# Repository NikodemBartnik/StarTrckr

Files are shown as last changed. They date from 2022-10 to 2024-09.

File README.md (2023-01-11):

## StarTracker - 3 axis astrophotography tracking solution

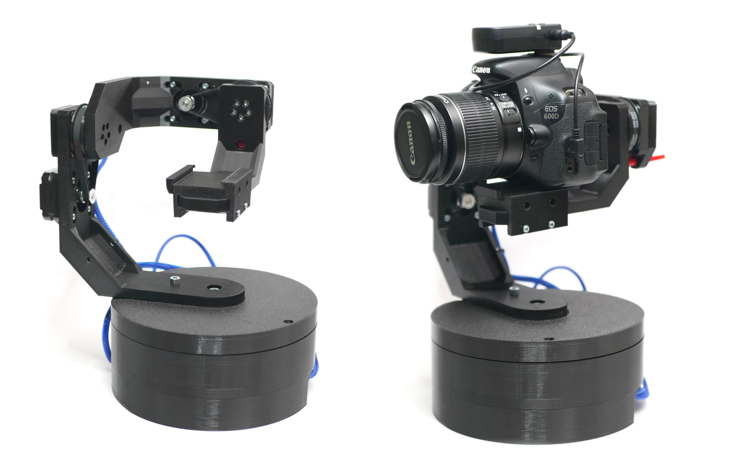
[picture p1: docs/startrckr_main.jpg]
startracker image


**Project is still in development and it may change!**<br>
Welcome to the StarTrckr project, an innovative solution to the problem of tracking in astrophotography. The goal of this project is to get over the limits of conventional tracking techniques so that hobbyists and enthusiasts can more easily take beautiful pictures of the night sky. Additionaly this construction enables for easier tracking of other objects (for example satellites) but the feature is not implemented yet.

A further benefit of the design is that it can be completely 3D printed, making it simple for everyone to construct and modify their own tracking device. It is planned to design an additional pro version that features steel parts for increased stiffness of the construction but 3D printed version will always stay as the bassis thats accesible and easy to replicate for everyone.

Since he was a young child, Nikodem Bartnik, the project's creator, has been fascinated about observing the night sky and space in general.  He is constantly searching for new ways to enhance the system and make it easier to use for users of all levels. At the same time he is into developing various open source projects and documenting the journeys of creating them on his YouTube channel. Additionaly is a part of Silesian Aerospace Technologies science club where together with friends he develops high altitude balloons, rockets and cubesat subsystems.

Designed by [Nikodem Bartnik](https://www.youtube.com/nikodembartnik). 

## Mechanics
Different design approaches have been considered and in the end multiple designs were created. Some of those are presented in the image below.
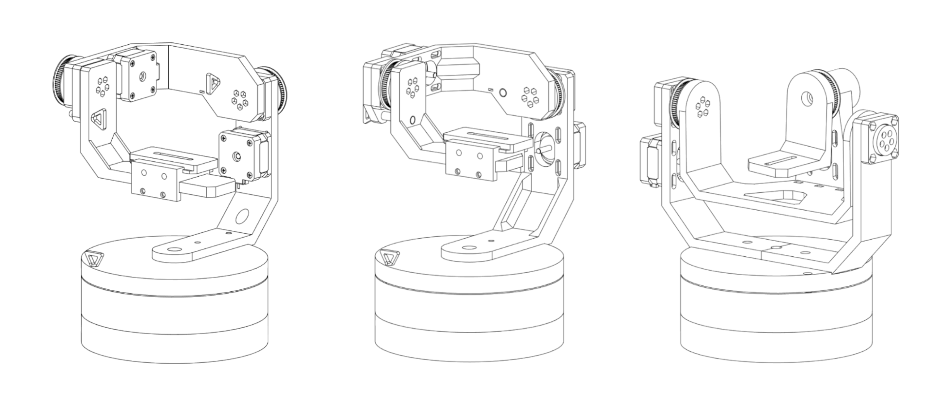
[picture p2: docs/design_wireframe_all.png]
StarTrckr designs

Most parts have been 3D printed and only a few additional parts like bearings, screws and motors are neccesary from the mechanical point of view. As of writing this readme there are three versions included in cad folder (v2, v3 nad v4). At this point v3 is prefered version and the one that is currently tested. Following list of printed parts reffers to v3.
| Name | Amount |
|---|---|
| arm1.3mf | 1 |
| arm2.3mf | 1 |
| arm3.3mf | 1 |
| base_pcb_box.3mf | 1 |
| base_motor_holder.3mf| 1 |
| base_gear.3mf | 1 |
| base_bearing_cap.3mf | 1 |
| base_gear_small.3mf  | 1 |
| gt2_pulley.3mf | 2 |
| shaft.3mf | 2 |
| shaft_cap.3mf | 2 |
| bearing_flap.3mf | 2 |
| quick_release_plate.3mf| 1 |
| quick_release1.3mf | 1 |
| quick_release2.3mf | 1 |
| pin.3mf | 3 |

List of additional parts needed for the mechanical assembly:
| Name | Amount | Description 
|---|---|---|
| Stepper motor 17HS08-1004S | 3 | Pancake type stepper motor, height: 20mm |
| 6205 bearing | 2 | ball bearing |
| 6804 bearing | 2 | ball bearing |
| GT2 belt 200mm | 2 | 6mm wide |
| GT2 pulley | 2 | 16 teeth |
| M6x60 screw | 1 |  |
| M6 nut | 1 | |
| M5 screws | a lot | lengths and amounts depend a lot on the version you are building |
| M5 nuts | a lot | |
| M3 screws | a lot | lengths and amounts depend a lot on the version you are building |
| M3 nuts | a lot | |

## Electronics
In the pcb folder all files regarding electronics for the project can be found. Everything was designed with KiCad, there is the schematic and PCB layout together with zip archives with gerber files for production and schematic in png format. Here is a table with all components required to assemble the PCB.
| Name | Amount | Description 
|---|---|---|
| RP2040 | 1 | Raspberry Pi microcontroller |
| A4988 | 3 | stepper driver, TMC2209 can be use as an upgrade to increase the accuracy |
| W25Q32JVSS | 1 | Flash memory |
| USB socket | 1 | type B |
| LM1117 | 1 | 3.3V linear voltage regulator |
| LED | 3 | size: 0805 preferably different color for each |
| Buzzer | 1 | THT, 12mm |
| 12MHz crystal | 1 | size: 5032 |
| 27 $\Omega$ resistor| 2 | size: 0603 |
| 100 $\Omega$ resistor|3 | size: 0603 |
| 1k $\Omega$ resistor | 2 | size: 0603 |
| 10k $\Omega$ resistor| 1 | size: 0603 |
| 27pF capacitor | 2 | size: 0603 |
| 1uF capacitor | 2 | size: 0603 |
| 10uF capacitor | 3 | size: 0603 |
| 100nF capacitor | 10 | size: 0603 |
| 2 pin screw terminal| 1 | |
| Some pin headers | | female and male, raster 2.54mm |

## Open Source
The StarTracker project is open-source, and the author welcomes feedback and contributions from the community. They believe that by sharing the project, they can help others to achieve the same level of success in capturing images of the night sky. If you are interested in building your own StarTrckr, the project's Github repository includes detailed instructions and all the necessary files to get started. Project was created as a bachelor thesis project at Silesian University of Technology and the created thesis can also be found in the repository as a PDF where one can read in depth about the research, problems and detailed explantion about the design process and decisions. 

## Software and firmware
Both were developed with Python programming language. As for now designed just as MVP to test basic functionality of the tractor will hopefully be developed more in the future.

## Testing
Example image untracked, f/5.6, ISO200, 600s, 55mm, Canon 600D after editing:
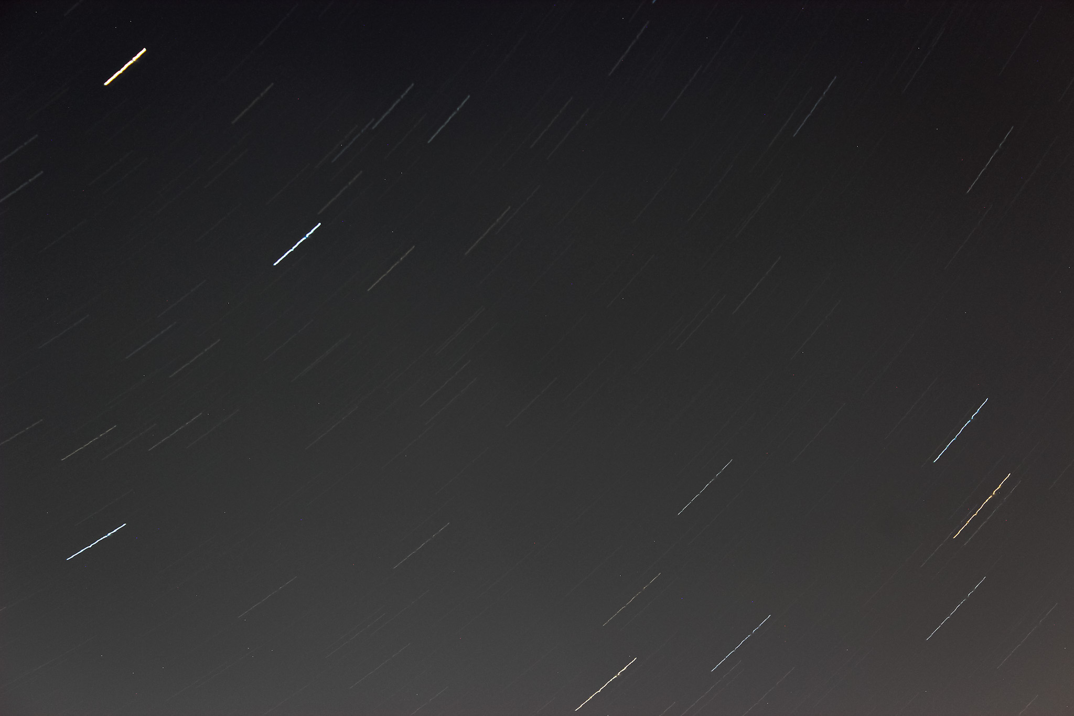
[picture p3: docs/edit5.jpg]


Example image with tracking enabled, same settings, camera and lens:

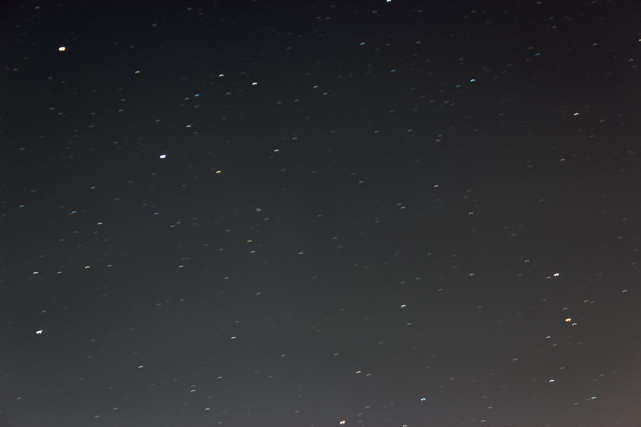
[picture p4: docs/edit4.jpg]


## Build Instruction
- todo 

## Project logo
<br>
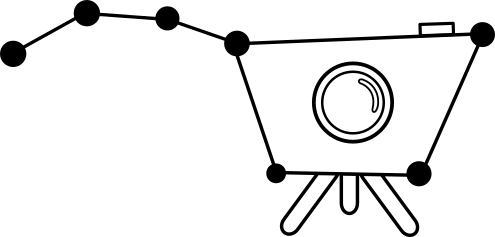
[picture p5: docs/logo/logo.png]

<br><br>

## About the author
Since I was a young child, I have been fascinated about observing the night sky and space in general. I am into developing various open source projects and documenting the journeys of creating them on my YouTube channel. Additionaly I am a part of Silesian Aerospace Technologies science club where together with friends we develop high altitude balloons, rockets and cubesat subsystems.

I hope you enjoy using the StarTracker and are able to capture stunning images of the night sky with it. The StarTracker project is an ongoing effort, and I am always looking for ways to improve it. Feel free to contact me or contribute to the project if you have any ideas or suggestions. Together, we can make astrophotography more accessible and enjoyable for everyone!

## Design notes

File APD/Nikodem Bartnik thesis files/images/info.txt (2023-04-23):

IMG_8831.JPG - tracked, f/5.6, ISO800, 240s, 55mm
IMG_8833.JPG - untracked, f/5.6, ISO800, 240s, 55mm
IMG_8858.JPG - tracked, f/5.6, ISO200, 600s, 55mm
IMG_8859.JPG - untracked, f/5.6, ISO200, 600s, 55mm
stacking_test.jpg - 22 90s exposures stacked together

_edit - versions edited with Lightroom

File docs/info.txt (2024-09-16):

IMG_8831.JPG - tracked, f/5.6, ISO800, 240s, 55mm
IMG_8833.JPG - untracked, f/5.6, ISO800, 240s, 55mm
IMG_8856.JPG - tracked, f/5.6, ISO200, 300s, 55mm
IMG_8857.JPG - untracked, f/5.6, ISO200, 300s, 55mm
IMG_8858.JPG - tracked, f/5.6, ISO200, 600s, 55mm
IMG_8859.JPG - untracked, f/5.6, ISO200, 600s, 55mm
IMG_8859.JPG to IMG_8883.JPG - tracked, f/5.6, ISO200, about 90s, 55mm

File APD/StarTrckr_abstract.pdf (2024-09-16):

### StarTrckr - 3 axis open-source night sky tracking device

Nikodem Bartnik
Silesian University of Technology, Poland

## Abstract

With advancements in digital photography and high-end equipment becoming less expensive, more and more amateurs are getting into astrophotography. Some of the work can be done with just a camera and a tripod but taking more advanced pictures, of objects that are light years away, require special equipment like star trackers, able to precisely compensate for Earth’s rotation, to capture long exposure images of the night sky. Usually, the equipment is expensive; thus, most amateurs can not afford it.

The aim of the project is to design and build an inexpensive, easy-to-build, and open-source star tracker. Relying on popular components that are easy to buy worldwide and 3D printed parts. The project’s reduction in cost and availability is just one component. The actual innovation of the approach is the use of a 3-axis system in conjunction with special algorithms to streamline workflow for the user as well as enable further advancement and facilitate tracking of other objects. StarTrckr is not mechanically aligned with the Earth’s rotation axis, unlike conventional solutions but it is also not susceptible to the issue of field rotation. The system can become totally autonomous, eliminating the need for manual polar alignment, with a few extra sensors added that are not present in the current version but are planned for the future.

Project was developed from scratch solely by the author including mechanical design, electronics design, and programming. Before the design stage began author performed research to find similar solutions and parts best suitable for the project. In order to test and validate the system’s performance, field tests were conducted at the very end and sample long exposure photos up to 600 seconds long were obtained.

StarTrckr was developed as a bachelor thesis project at the Silesian University of Technology and was successfully defended in February 2023. Further development of the projects is planned by the author to create a completely automatic solution and improve the biggest flows of the design. Since the beginning of the project, it was decided that it will be open source and shared with everyone for free to contribute to the development of astrophotography. All files and description of the project can be found on GitHub where it is regularly updated as the work progresses.

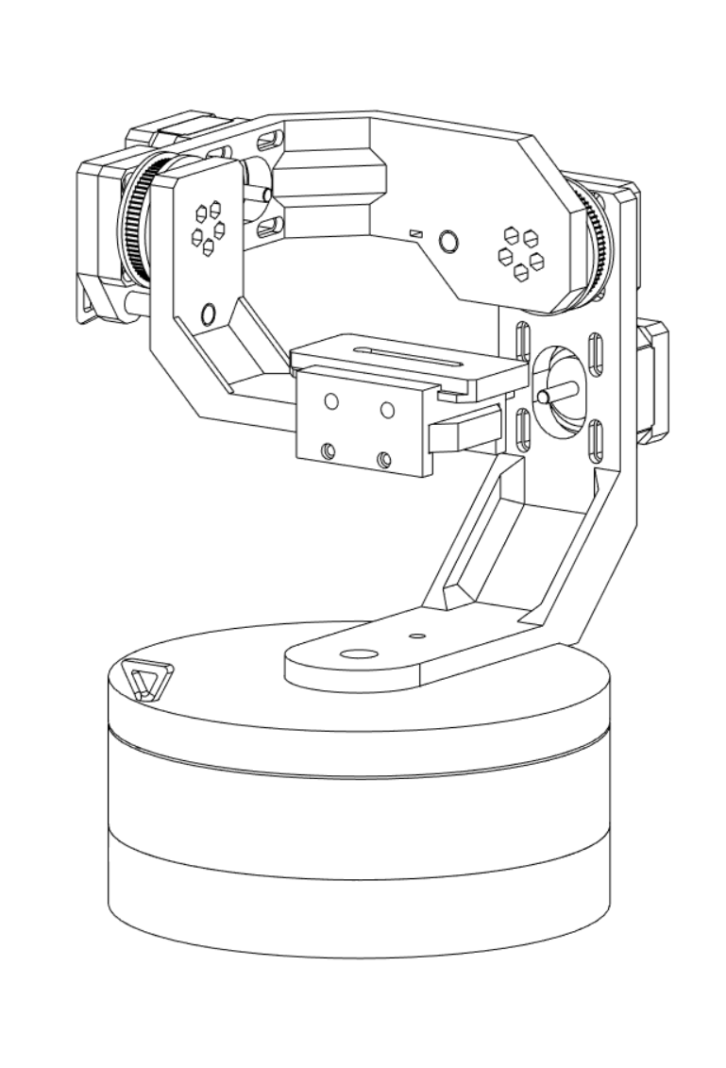
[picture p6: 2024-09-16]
docs/thesis/design/design_wireframe_v3.png

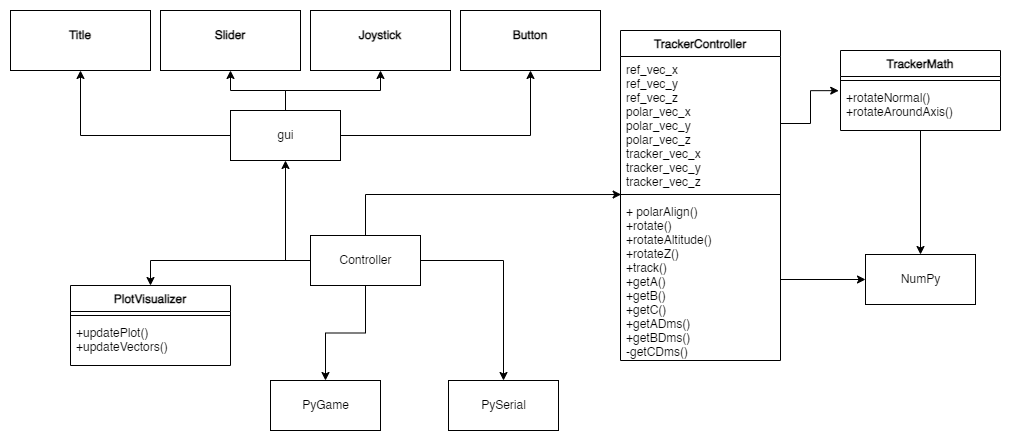
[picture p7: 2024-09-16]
docs/thesis/desktop_software_uml.png

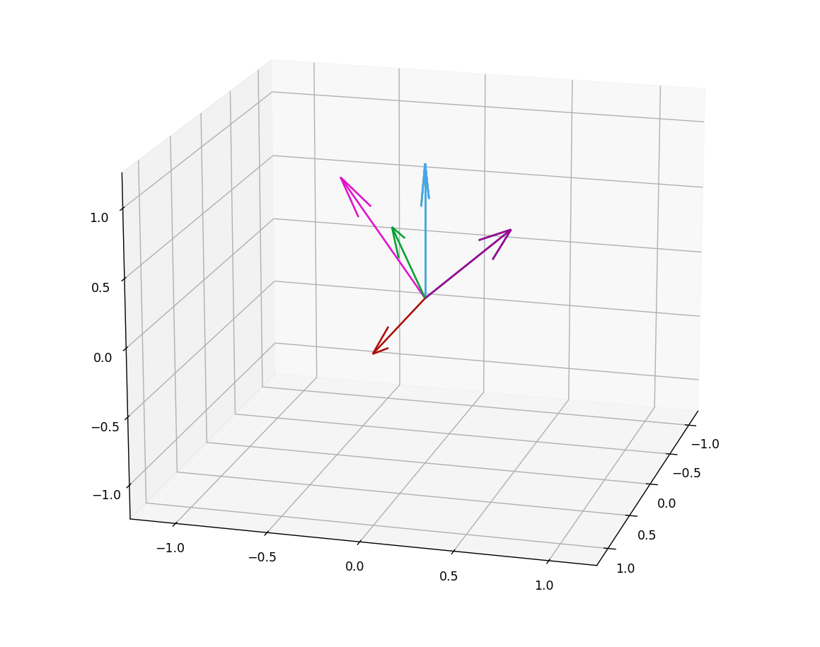
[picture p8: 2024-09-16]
docs/thesis/plot_vectors_2.png

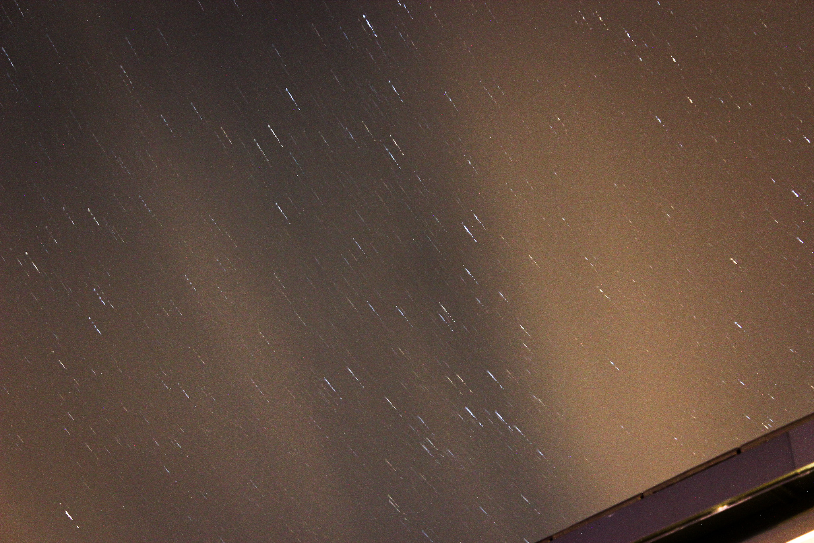
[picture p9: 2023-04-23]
APD/Nikodem Bartnik thesis files/images/IMG_8833_edit.jpg

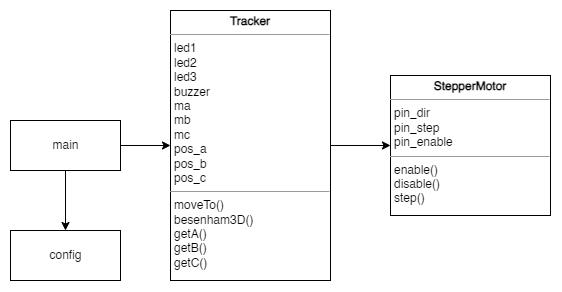
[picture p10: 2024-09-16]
docs/thesis/firmware_uml.png

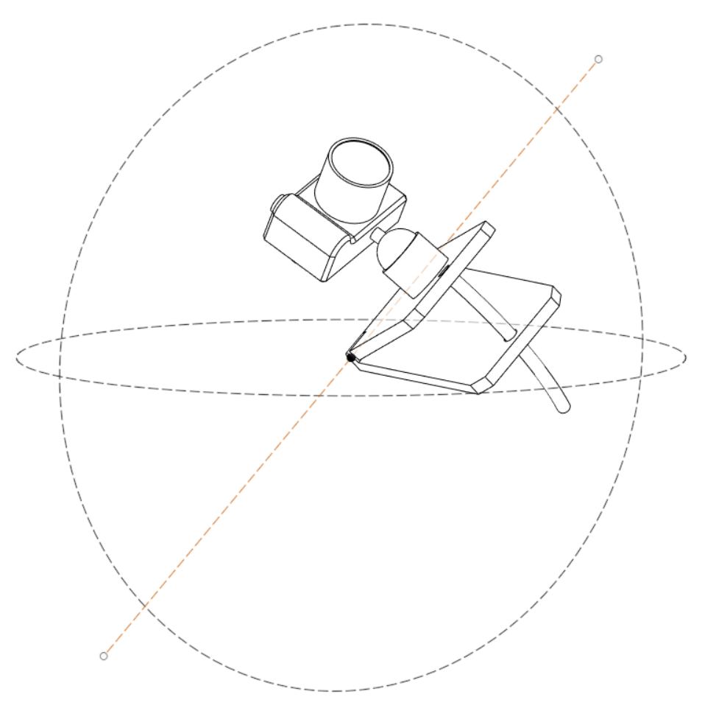
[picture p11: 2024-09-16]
docs/thesis/barndoortracker.png

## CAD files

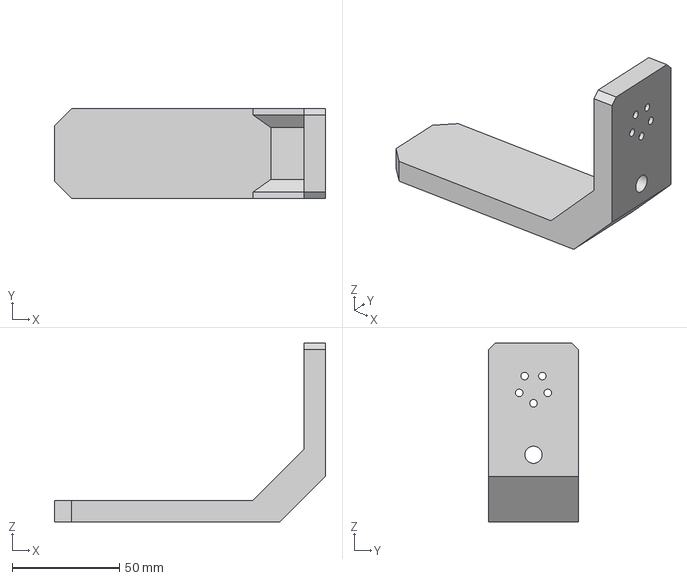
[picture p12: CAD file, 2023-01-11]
APD/Nikodem Bartnik thesis files/3d printed parts/arm3.3mf
126.2 x 42.0 x 83.2 mm

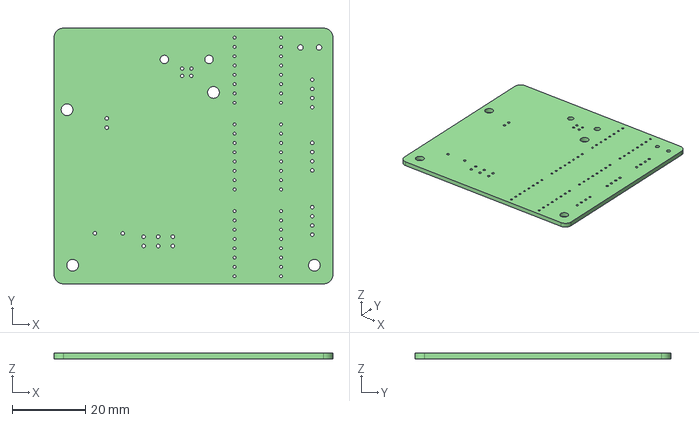
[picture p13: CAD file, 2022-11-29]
APD/Nikodem Bartnik thesis files/pcb/startrckr_pcb.step
76.2 x 69.9 x 1.60 mm

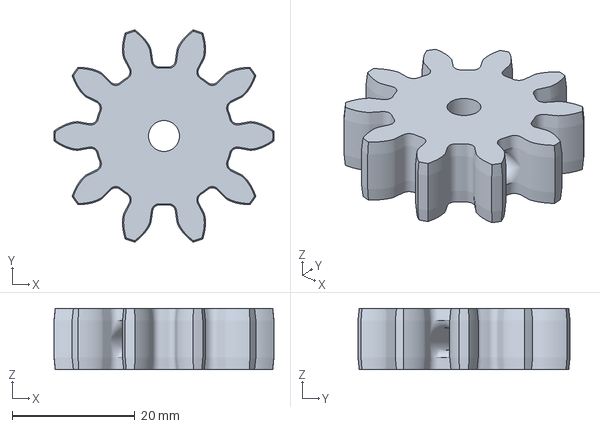
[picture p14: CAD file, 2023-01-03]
cad/v4/base gear small.3mf
35.8 x 34.5 x 10.0 mm

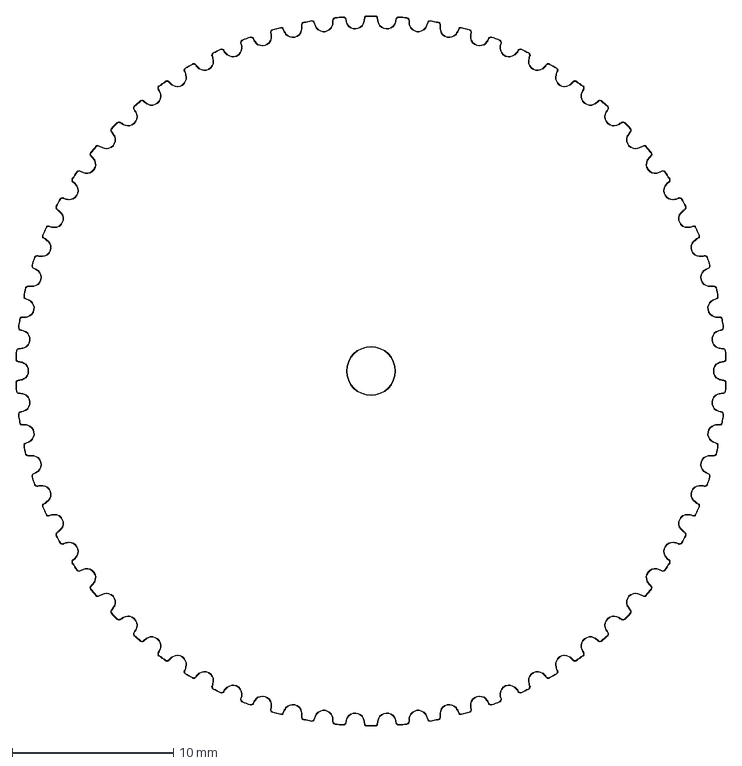
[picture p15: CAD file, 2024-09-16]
docs/gt2 gear/1.dxf
44.1 x 44.1 mm

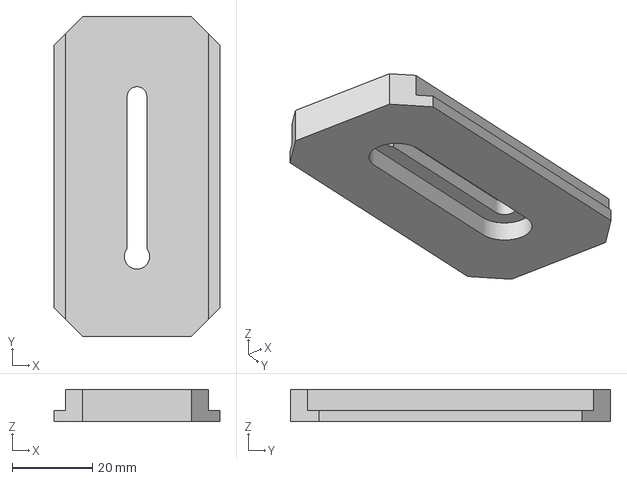
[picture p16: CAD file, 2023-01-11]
APD/Nikodem Bartnik thesis files/3d printed parts/quick release plate.3mf
41.4 x 80.0 x 8.00 mm

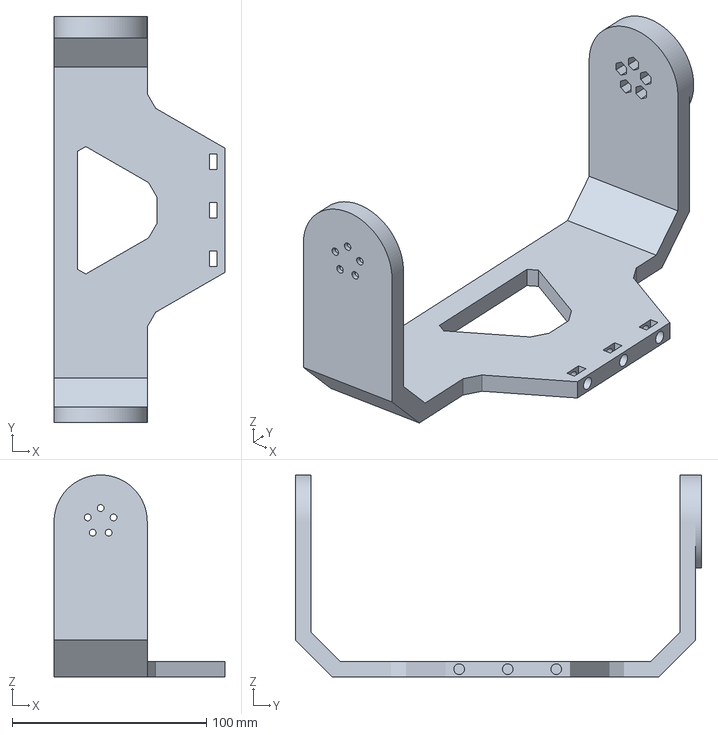
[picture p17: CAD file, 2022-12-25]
cad/v4/arm2.3mf
88.0 x 209.1 x 104.0 mm

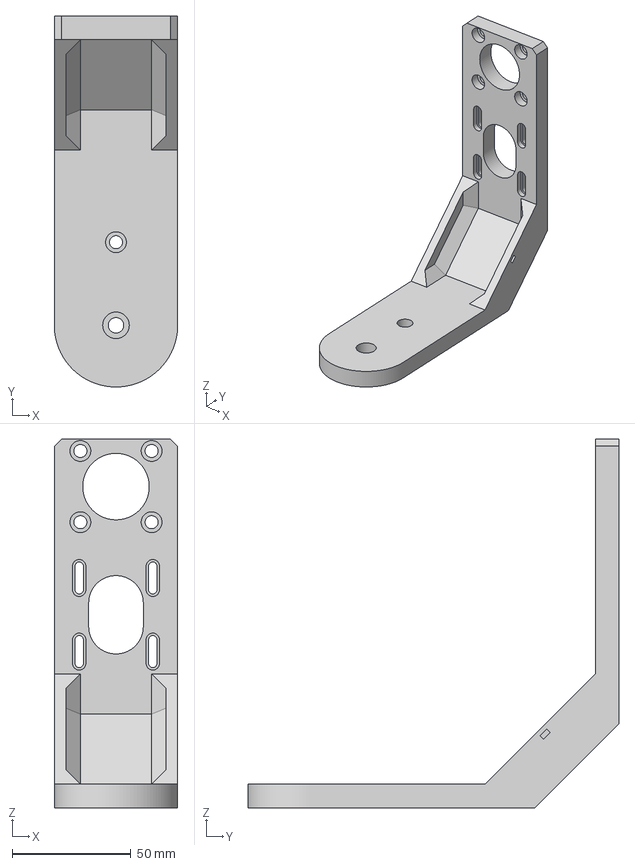
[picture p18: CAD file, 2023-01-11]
APD/Nikodem Bartnik thesis files/3d printed parts/arm1.3mf
52.0 x 156.3 x 155.4 mm

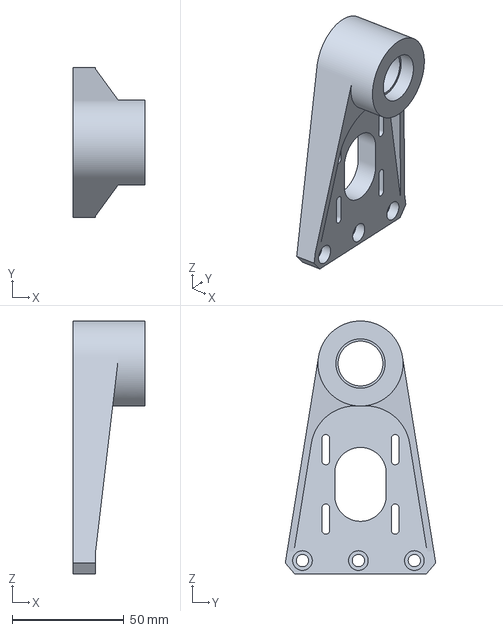
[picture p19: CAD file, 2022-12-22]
cad/v4/rotator plate.3mf
32.0 x 67.2 x 113.0 mm

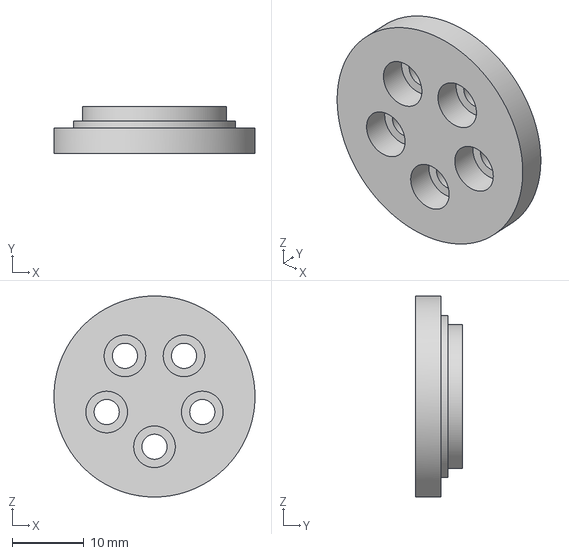
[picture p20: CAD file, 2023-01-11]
APD/Nikodem Bartnik thesis files/3d printed parts/shaft2.3mf
28.0 x 6.50 x 28.0 mm

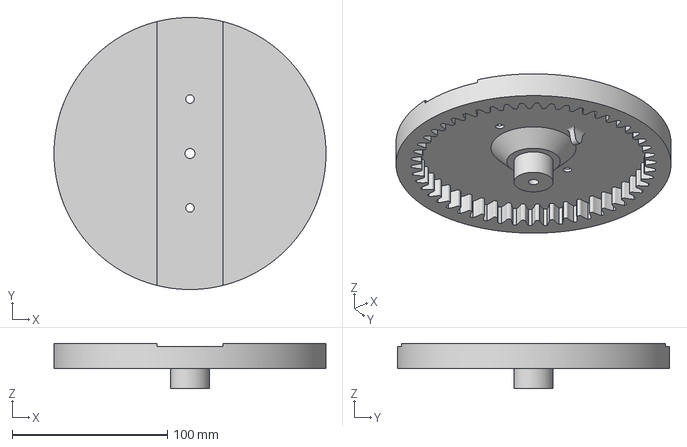
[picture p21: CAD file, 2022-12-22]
cad/v4/base gear.3mf
175.0 x 175.0 x 29.0 mm

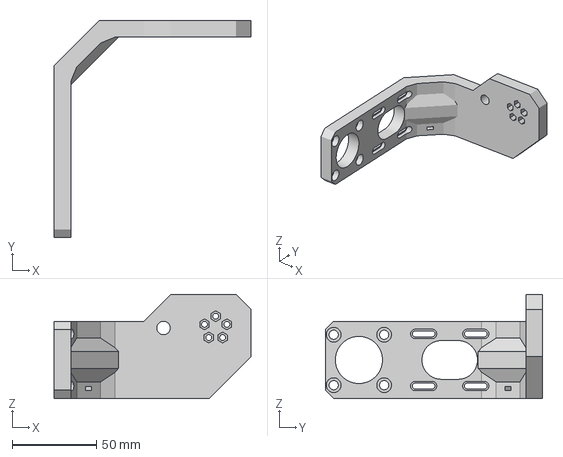
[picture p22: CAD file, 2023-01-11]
APD/Nikodem Bartnik thesis files/3d printed parts/arm2.3mf
117.2 x 129.3 x 62.0 mm

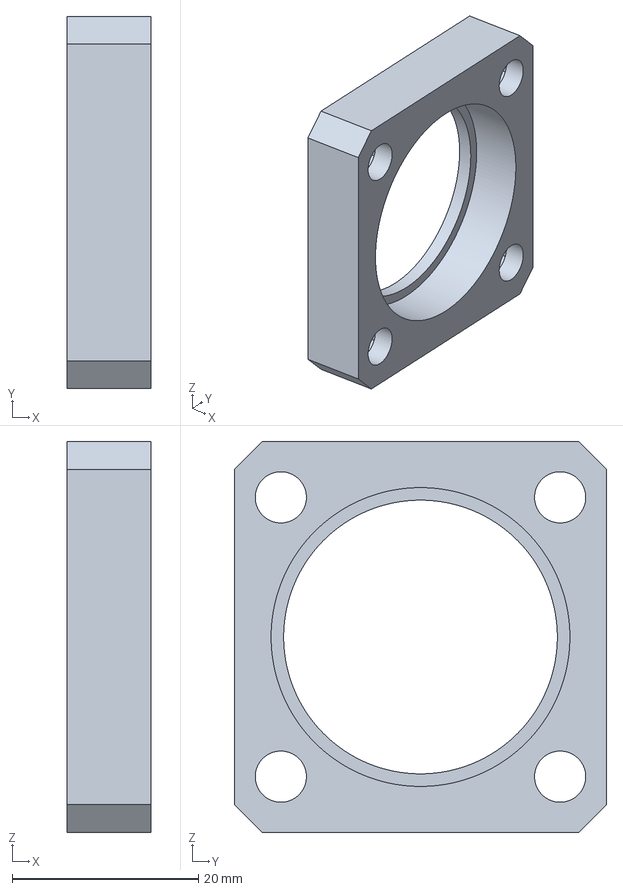
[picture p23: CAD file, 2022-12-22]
cad/v4/bearing flap.3mf
9.00 x 40.0 x 42.0 mm

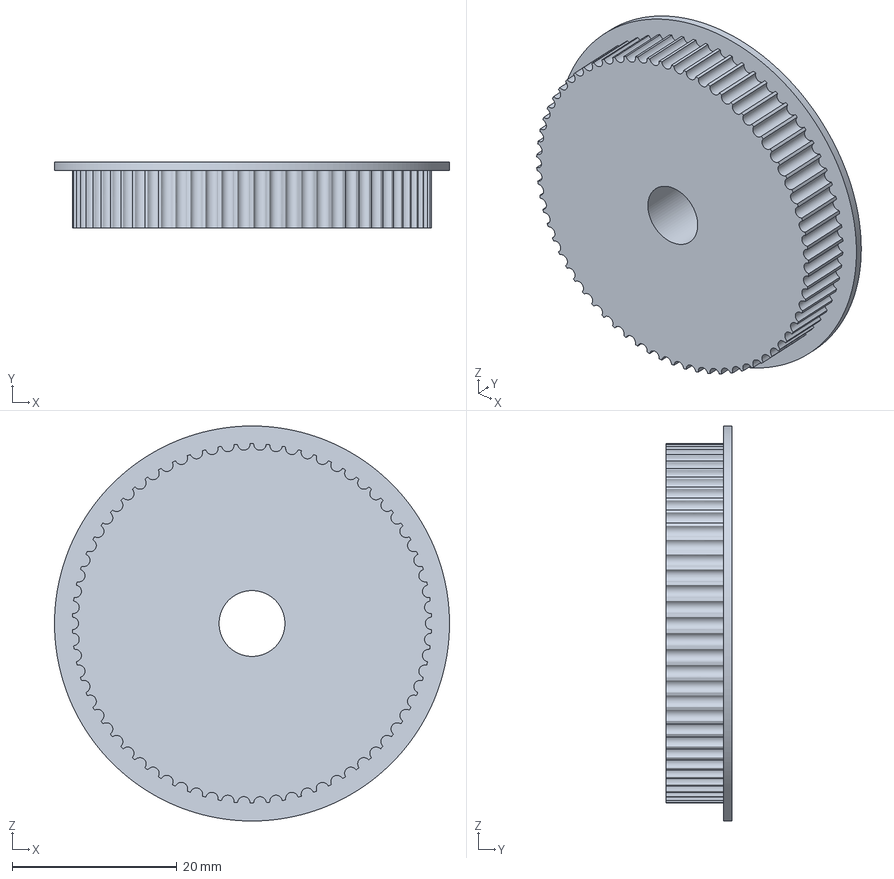
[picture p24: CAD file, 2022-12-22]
cad/v4/rotator pulley.3mf
48.0 x 8.00 x 48.0 mm

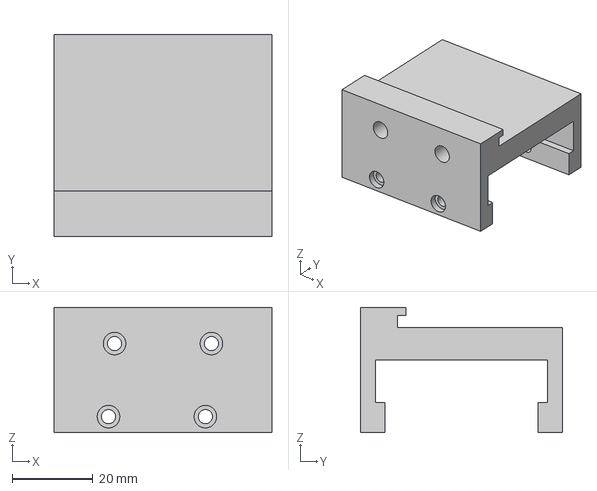
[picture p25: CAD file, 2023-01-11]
APD/Nikodem Bartnik thesis files/3d printed parts/quick release 1.3mf
54.0 x 50.0 x 31.0 mm

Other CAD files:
APD/Nikodem Bartnik thesis files/3d printed parts/base gear.3mf
cad/v4/base motor holder.3mf
APD/Nikodem Bartnik thesis files/3d printed parts/base bearing cap.3mf
cad/v4/arm1_1.3mf
APD/Nikodem Bartnik thesis files/3d printed parts/base PCB box.3mf
APD/Nikodem Bartnik thesis files/3d printed parts/base gear small.3mf
APD/Nikodem Bartnik thesis files/3d printed parts/base motor holder.3mf
APD/Nikodem Bartnik thesis files/3d printed parts/bearing flap.3mf
APD/Nikodem Bartnik thesis files/3d printed parts/gt2 pulley.3mf
APD/Nikodem Bartnik thesis files/3d printed parts/pin.3mf
APD/Nikodem Bartnik thesis files/3d printed parts/quick release 2.3mf
APD/Nikodem Bartnik thesis files/3d printed parts/shaft1.3mf
cad/v2/arm1.3mf
cad/v2/arm2.3mf
cad/v2/arm3.3mf
cad/v2/base gear small.3mf
cad/v2/base gear.3mf
cad/v2/bearing flap.3mf
cad/v2/gt2 pulley.3mf
cad/v2/quick release 1.3mf
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

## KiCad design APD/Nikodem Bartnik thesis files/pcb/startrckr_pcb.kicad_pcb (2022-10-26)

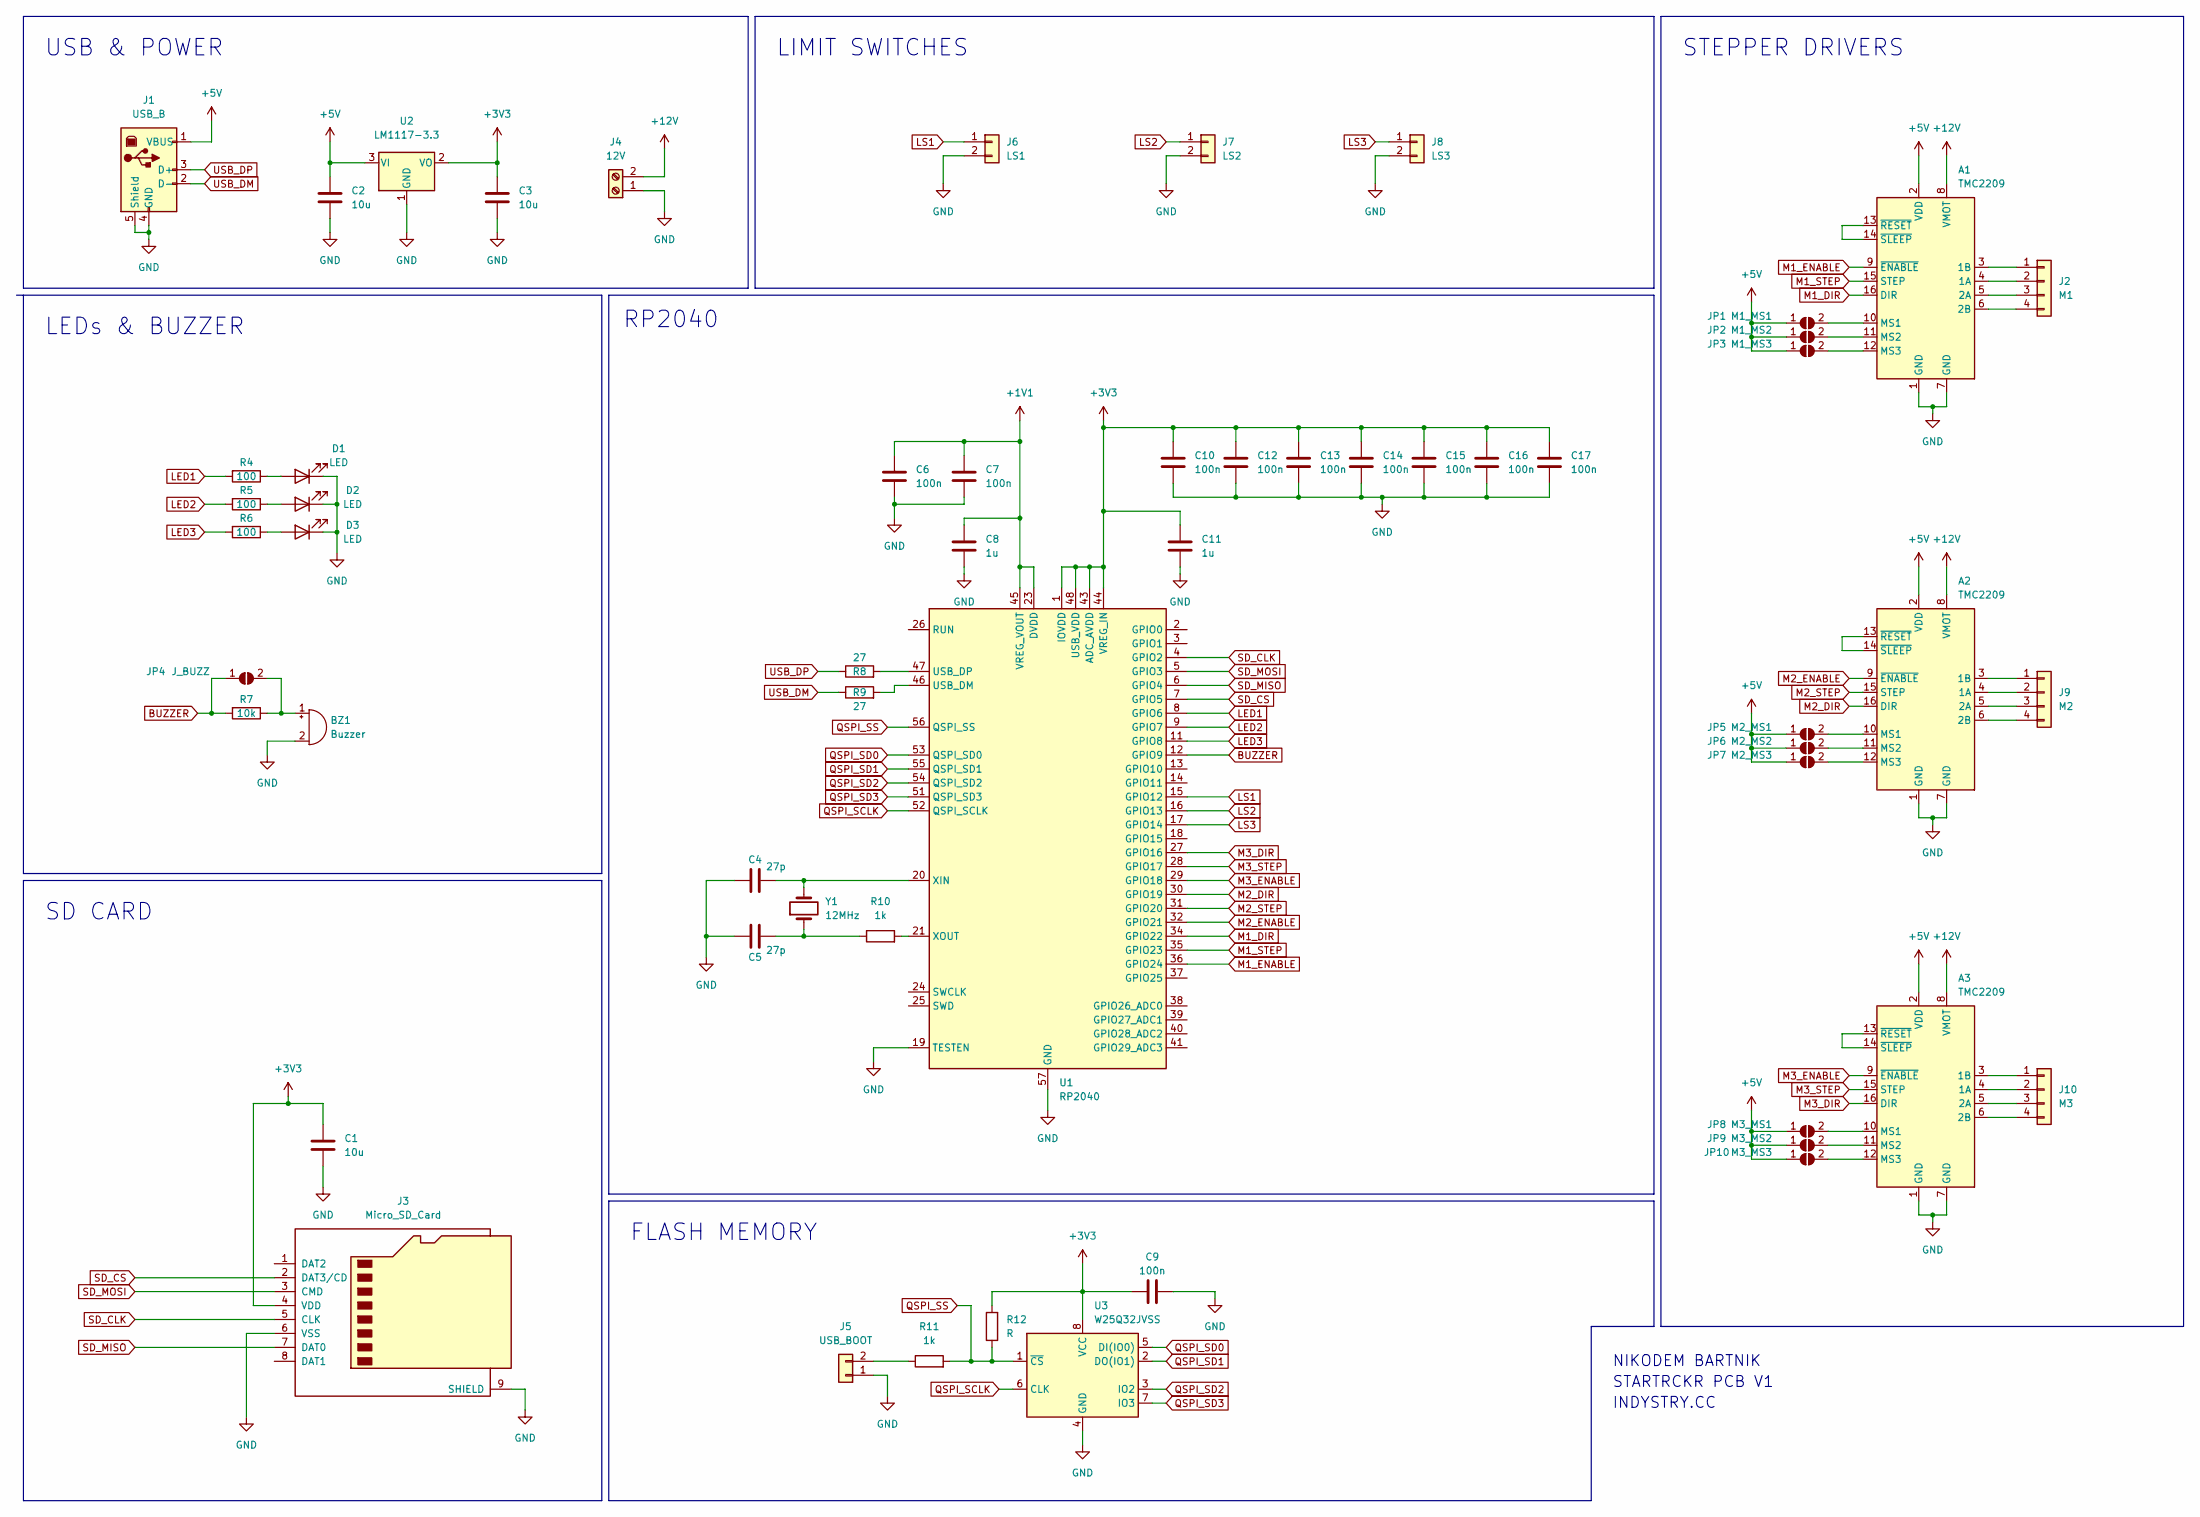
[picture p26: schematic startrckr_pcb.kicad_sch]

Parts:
A1, A2, A3: TMC2209; Pololu_Breakout-16_15.2x20.3mm
BZ1: Buzzer; Buzzer_12x9.5RM7.6
C1, C2, C3: 10u; C_0603_1608Metric_Pad1.08x0.95mm_HandSolder
C4, C5: 27p; C_0603_1608Metric_Pad1.08x0.95mm_HandSolder
C6, C7, C9, C10, C12, C13, C14, C15, C16, C17: 100n; C_0603_1608Metric_Pad1.08x0.95mm_HandSolder
C8, C11: 1u; C_0603_1608Metric_Pad1.08x0.95mm_HandSolder
D1, D2, D3: LED; LED_0805_2012Metric_Pad1.15x1.40mm_HandSolder
J1: USB_B; U-USBBR04P-F000
J2: M1; JST_XH_B4B-XH-A_1x04_P2.50mm_Vertical
J3: Micro_SD_Card; microSD_HC_Wuerth_693072010801
J4: 12V; TerminalBlock_bornier-2_P5.08mm
J5: USB_BOOT; PinHeader_1x02_P2.54mm_Vertical
J6: LS1; PinSocket_1x02_P2.54mm_Vertical
J7: LS2; PinSocket_1x02_P2.54mm_Vertical
J8: LS3; PinSocket_1x02_P2.54mm_Vertical
J9: M2; JST_XH_B4B-XH-A_1x04_P2.50mm_Vertical
J10: M3; JST_XH_B4B-XH-A_1x04_P2.50mm_Vertical
JP1: M1_MS1; SolderJumper-2_P1.3mm_Open_Pad1.0x1.5mm
JP2: M1_MS2; SolderJumper-2_P1.3mm_Open_Pad1.0x1.5mm
JP3: M1_MS3; SolderJumper-2_P1.3mm_Open_Pad1.0x1.5mm
JP4: J_BUZZ; SolderJumper-2_P1.3mm_Open_Pad1.0x1.5mm
JP5: M2_MS1; SolderJumper-2_P1.3mm_Open_Pad1.0x1.5mm
JP6: M2_MS2; SolderJumper-2_P1.3mm_Open_Pad1.0x1.5mm
JP7: M2_MS3; SolderJumper-2_P1.3mm_Open_Pad1.0x1.5mm
JP8: M3_MS1; SolderJumper-2_P1.3mm_Open_Pad1.0x1.5mm
JP9: M3_MS2; SolderJumper-2_P1.3mm_Open_Pad1.0x1.5mm
JP10: M3_MS3; SolderJumper-2_P1.3mm_Open_Pad1.0x1.5mm
R4, R5, R6: 100; R_0603_1608Metric_Pad0.98x0.95mm_HandSolder
R7: 10k; R_0603_1608Metric_Pad0.98x0.95mm_HandSolder
R8, R9: 27; R_0603_1608Metric_Pad0.98x0.95mm_HandSolder
R10, R11: 1k; R_0603_1608Metric_Pad0.98x0.95mm_HandSolder
R12: R; R_0603_1608Metric_Pad0.98x0.95mm_HandSolder
U1: RP2040; QFN-56-1EP_7x7mm_P0.4mm_EP3.2x3.2mm
U2: LM1117-3.3; SOT-223-3_TabPin2
U3: W25Q32JVSS; SOIC-8_5.23x5.23mm_P1.27mm
Y1: 12MHz; Crystal_SMD_5032-2Pin_5.0x3.2mm

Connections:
+1V1: C6.1, C7.1, C8.1, U1.23 (DVDD), U1.45 (VREG_VOUT), U1.50 (DVDD)
+3V3: C1.1, C3.1, C9.1, C10.1, C11.1, C12.1, C13.1, C14.1, C15.1, C16.1, C17.1, J3.4 (VDD), R12.2, U1.1 (IOVDD), U1.10 (IOVDD), U1.22 (IOVDD), U1.33 (IOVDD), U1.42 (IOVDD), U1.43 (ADC_AVDD), U1.44 (VREG_IN), U1.48 (USB_VDD), U1.49 (IOVDD), U2.2 (VO), U3.8 (VCC)
+5V: A1.2 (VDD), A2.2 (VDD), A3.2 (VDD), C2.1, J1.1 (VBUS), JP1.1 (A), JP2.1 (A), JP3.1 (A), JP5.1 (A), JP6.1 (A), JP7.1 (A), JP8.1 (A), JP9.1 (A), JP10.1 (A), U2.3 (VI)
+12V: A1.8 (VMOT), A2.8 (VMOT), A3.8 (VMOT), J4.2
BUZZER: JP4.1 (A), R7.2, U1.12 (GPIO9)
GND: A1.1 (GND), A1.7 (GND), A2.1 (GND), A2.7 (GND), A3.1 (GND), A3.7 (GND), BZ1.2 (+), C1.2, C2.2, C3.2, C4.1, C5.1, C6.2, C7.2, C8.2, C9.2, C10.2, C11.2, C12.2, C13.2, C14.2, C15.2, C16.2, C17.2, D1.1 (K), D2.1 (K), D3.1 (K), J1.4 (GND), J1.5 (Shield), J3.6 (VSS), J3.9 (SHIELD), J4.1, J5.1, J6.2, J7.2, J8.2, U1.19 (TESTEN), U1.57 (GND), U2.1 (GND), U3.4 (GND)
LED1: R4.2, U1.8 (GPIO6)
LED2: R5.2, U1.9 (GPIO7)
LED3: R6.2, U1.11 (GPIO8)
LS1: J6.1, U1.15 (GPIO12)
LS2: J7.1, U1.16 (GPIO13)
LS3: J8.1, U1.17 (GPIO14)
M1_DIR: A1.16 (DIR), U1.34 (GPIO22)
M1_ENABLE: A1.9 (~ENABLE), U1.36 (GPIO24)
M1_STEP: A1.15 (STEP), U1.35 (GPIO23)
M2_DIR: A2.16 (DIR), U1.30 (GPIO19)
M2_ENABLE: A2.9 (~ENABLE), U1.32 (GPIO21)
M2_STEP: A2.15 (STEP), U1.31 (GPIO20)
M3_DIR: A3.16 (DIR), U1.27 (GPIO16)
M3_ENABLE: A3.9 (~ENABLE), U1.29 (GPIO18)
M3_STEP: A3.15 (STEP), U1.28 (GPIO17)
unnamed: A1.3 (1B), J2.1
unnamed: A1.4 (1A), J2.2
unnamed: A1.5 (2A), J2.3
unnamed: A1.6 (2B), J2.4
unnamed: A1.10 (MS1), JP1.2 (B)
unnamed: A1.11 (MS2), JP2.2 (B)
unnamed: A1.12 (MS3), JP3.2 (B)
unnamed: A1.13 (~RESET), A1.14 (~SLEEP)
unnamed: A2.3 (1B), J9.1
unnamed: A2.4 (1A), J9.2
unnamed: A2.5 (2A), J9.3
unnamed: A2.6 (2B), J9.4
unnamed: A2.10 (MS1), JP5.2 (B)
unnamed: A2.11 (MS2), JP6.2 (B)
unnamed: A2.12 (MS3), JP7.2 (B)
unnamed: A2.13 (~RESET), A2.14 (~SLEEP)
unnamed: A3.3 (1B), J10.1
unnamed: A3.4 (1A), J10.2
unnamed: A3.5 (2A), J10.3
unnamed: A3.6 (2B), J10.4
unnamed: A3.10 (MS1), JP8.2 (B)
unnamed: A3.11 (MS2), JP9.2 (B)
unnamed: A3.12 (MS3), JP10.2 (B)
unnamed: A3.13 (~RESET), A3.14 (~SLEEP)
unnamed: BZ1.1 (-), JP4.2 (B), R7.1
unnamed: C4.2, U1.20 (XIN), Y1.2
unnamed: C5.2, R10.1, Y1.1
unnamed: D1.2 (A), R4.1
unnamed: D2.2 (A), R5.1
unnamed: D3.2 (A), R6.1
unnamed: J5.2, R11.1
unnamed: R8.2, U1.47 (USB_DP)
unnamed: R9.2, U1.46 (USB_DM)
unnamed: R10.2, U1.21 (XOUT)
QSPI_SCLK: U1.52 (QSPI_SCLK), U3.6 (CLK)
QSPI_SD0: U1.53 (QSPI_SD0), U3.5 (DI(IO0))
QSPI_SD1: U1.55 (QSPI_SD1), U3.2 (DO(IO1))
QSPI_SD2: U1.54 (QSPI_SD2), U3.3 (IO2)
QSPI_SD3: U1.51 (QSPI_SD3), U3.7 (IO3)
QSPI_SS: R11.2, R12.1, U1.56 (QSPI_SS), U3.1 (~CS)
SD_CLK: J3.5 (CLK), U1.4 (GPIO2)
SD_CS: J3.2 (DAT3/CD), U1.7 (GPIO5)
SD_MISO: J3.7 (DAT0), U1.6 (GPIO4)
SD_MOSI: J3.3 (CMD), U1.5 (GPIO3)
USB_DM: J1.2 (D-), R9.1
USB_DP: J1.3 (D+), R8.1

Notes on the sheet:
STARTRCKR PCB V1
LIMIT SWITCHES
NIKODEM BARTNIK
INDYSTRY.CC
FLASH MEMORY
STEPPER DRIVERS
LEDs & BUZZER
USB & POWER
RP2040
SD CARD

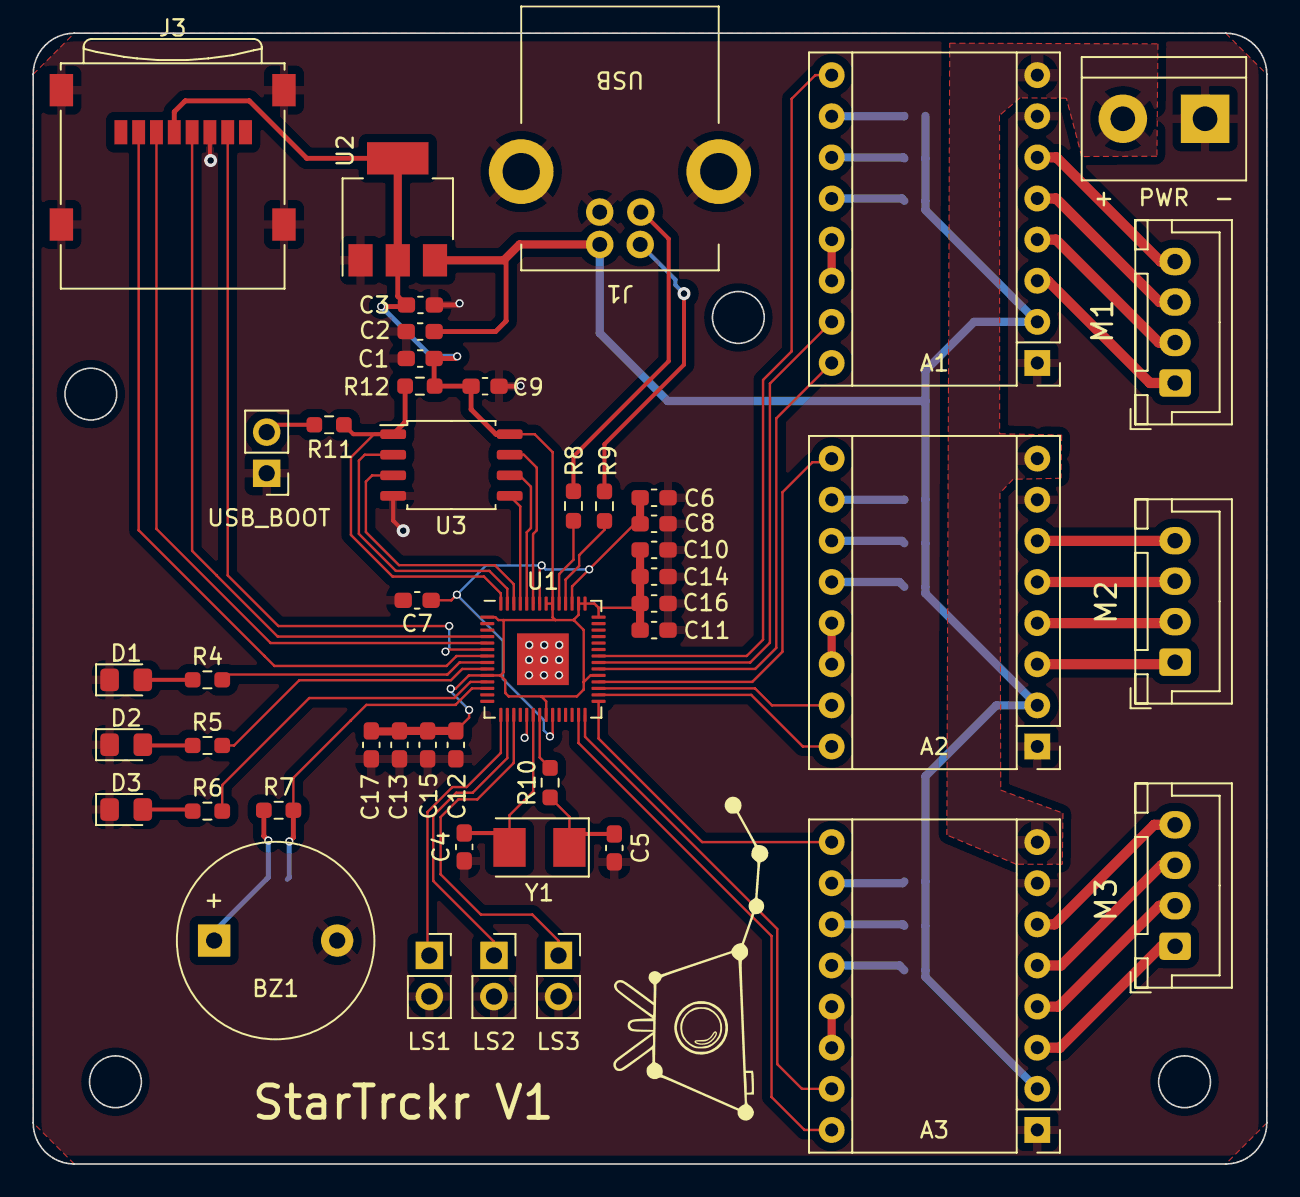
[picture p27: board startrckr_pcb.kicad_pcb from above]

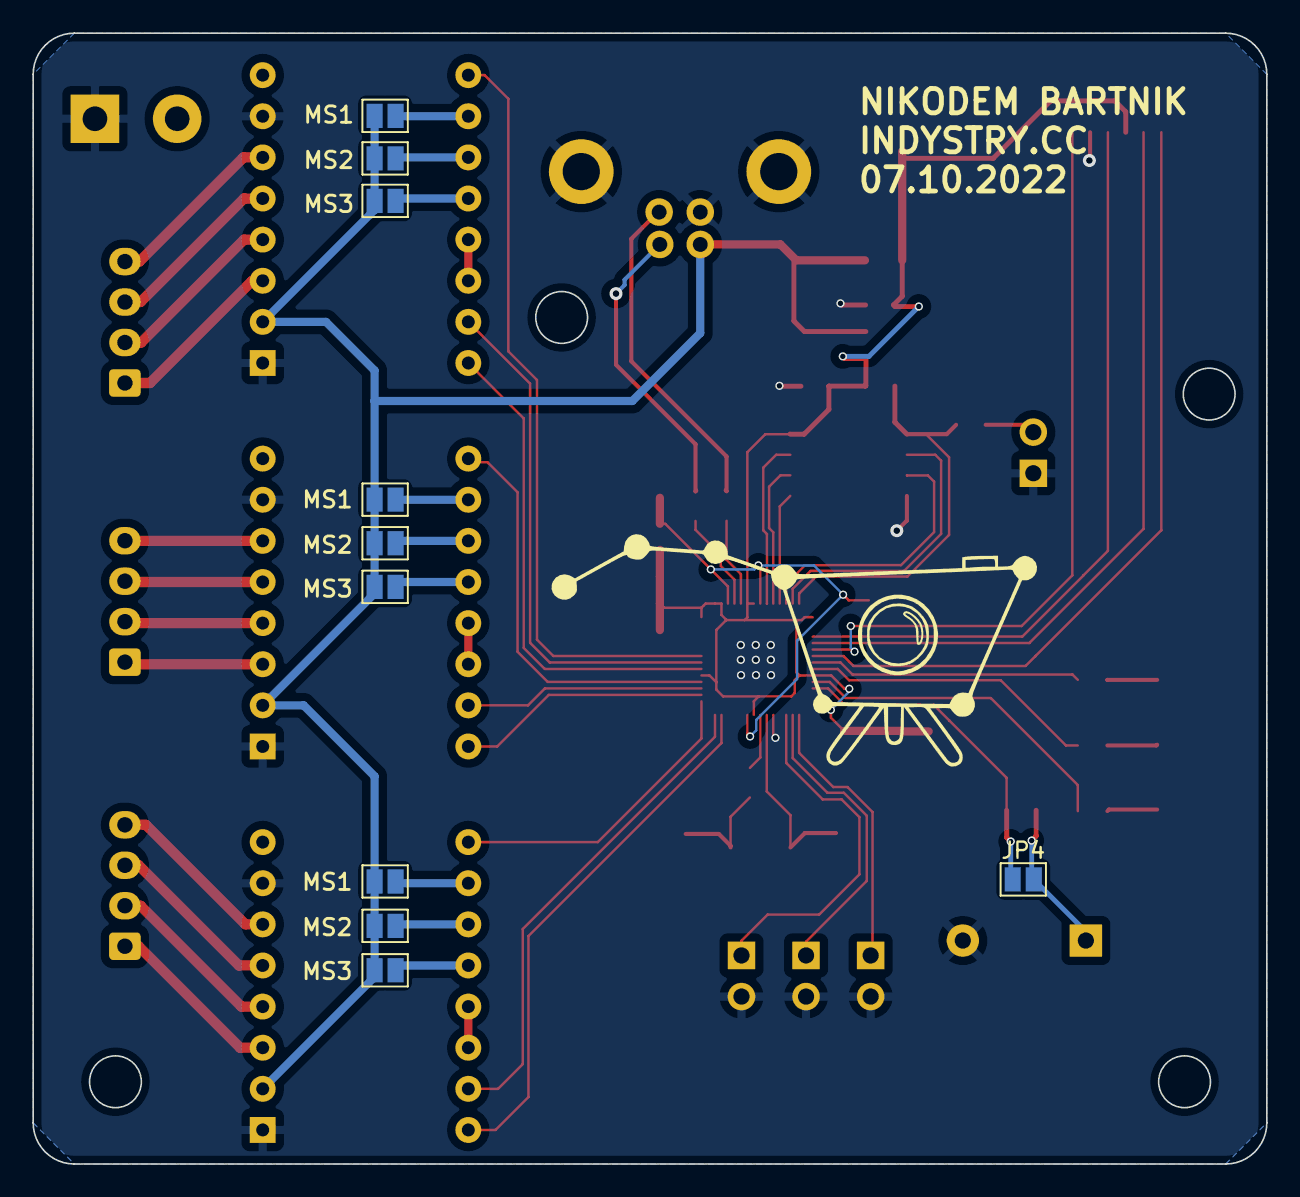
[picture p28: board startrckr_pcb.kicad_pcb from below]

Board: 2 copper layers, 76.2 x 69.9 mm, 57 parts (10 on the bottom side), 67 nets.

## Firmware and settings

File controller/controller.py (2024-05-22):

import pygame, time, gui
import serial
import TrackerController
import PlotVisualizer

pygame.init()
screen = pygame.display.set_mode([800, 600])

SERIALPORT ='/dev/cu.usbmodem14201'
tracker = serial.Serial(SERIALPORT, 115200, timeout=0.01)

mousePressed = False
tc = TrackerController.TrackerController()
plotVisualizer = None
setAxis = False

### CHANGE PARAMETERS HERE ###
LATITUDE = 50.4672
LONGITUDE = 18.7276

def clickCheck(pos, clicked):
    joystick.checkIfPressed(pos, clicked)
    button_turn_left.checkIfPressed(pos, clicked)
    button_turn_right.checkIfPressed(pos, clicked)
    button_set_axis.checkIfPressed(pos, clicked)
    button_track.checkIfPressed(pos, clicked)
    slider_movement_precision.checkIfPressed(pos, clicked)

def drawAll():
    joystick.draw(screen)
    button_turn_left.draw(screen)
    button_turn_right.draw(screen)
    title_turn.draw(screen)
    titleL.draw(screen)
    titleR.draw(screen)
    title_set_axis.draw(screen)
    button_set_axis.draw(screen)
    title_track.draw(screen)
    button_track.draw(screen)
    title_angle.draw(screen)
    slider_movement_precision.draw(screen)
    title_a_pos.draw(screen)
    title_b_pos.draw(screen)
    title_c_pos.draw(screen)
    title_ra_dec.draw(screen)


def WaitForOK():
    while(1):
        if(tracker.readline() == b'OK\n'):
            break


joystick = gui.Joystick((260,200), 120)
title_turn = gui.Title((590,60), 'Turn')
titleL = gui.Title((545,120), 'L')
titleR = gui.Title((675,120), 'R')
button_turn_left = gui.Button((550, 130), 30, False, False)
button_turn_right = gui.Button((680, 130), 30, False, False)
title_set_axis = gui.Title((520, 210), 'Set axis')
button_set_axis = gui.Button((650, 220), 20, False, False)
title_track = gui.Title((520, 280), 'Track')
button_track = gui.Button((650, 290), 20, False, True)
title_angle = gui.Title((580, 340), 'set axis')
slider_movement_precision = gui.Slider((100, 380), 300, 0.5, 0, 1)
title_a_pos = gui.Title((480, 420), '0')
title_b_pos = gui.Title((480, 450), '0')
title_c_pos = gui.Title((480, 480), '0')
title_ra_dec = gui.Title((480, 510), '0')

last_tracking_update = 0


while 1:
    keyPressed = pygame.key.get_pressed()
    screen.fill((40,40,40))
    for event in pygame.event.get():
        if event.type == pygame.MOUSEBUTTONDOWN:
            mousePressed = True
        if event.type == pygame.MOUSEBUTTONUP:
            mousePressed = False
        if event.type == pygame.QUIT:
            pygame.quit()
        clickCheck(pygame.mouse.get_pos(), mousePressed)
        
    drawAll()
    a = joystick.getValue()
    movementPrecision = slider_movement_precision.getValue()
    if (a[0] > 50 and a[0] < 130 and a[1] > 0.5) or keyPressed[pygame.K_UP]:
        tc.rotateAltitude(-movementPrecision)
    if (a[0] > 230 and a[0] < 310 and a[1] > 0.5) or keyPressed[pygame.K_DOWN]:
        tc.rotateAltitude(movementPrecision)

    if (a[0] > 140 and a[0] < 210 and a[1] > 0.5) or keyPressed[pygame.K_RIGHT]:
        tc.rotateAzimuth(movementPrecision)
    if (a[0] > 320 or a[0] < 40 and a[1] > 0.5) or keyPressed[pygame.K_LEFT]:
       tc.rotateAzimuth(-movementPrecision)

    if button_turn_right.getValue():
        tc.rotateField(-movementPrecision)
    if button_turn_left.getValue():
        tc.rotateField(movementPrecision)

    if button_set_axis.getValue():
        tc.polarAlign()
        #plotVisualizer = PlotVisualizer.PlotVisualizer(tc.getRefVecX(), tc.getRefVecZ(), tc.getPolarVecX(), tc.getPolarVecZ(), tc.getTrackerVecX(), tc.getTrackerVecZ())
        setAxis = True
        title_angle.change('Axis ready!')

    if button_track.getValue():
        if last_tracking_update == 0:
            pass
        else:
            #86164
            tc.track(((time.time() - last_tracking_update)/86164 * 360))
        last_tracking_update = time.time()

    
    #if(setAxis):
        #plotVisualizer.updateVectors(tc.getRefVecX(), tc.getRefVecZ(), tc.getPolarVecX(), tc.getPolarVecZ(), tc.getTrackerVecX(), tc.getTrackerVecZ(), tc.getC(), tc.getB(), tc.getA())
        
    try:
        title_a_pos.change('ALT: ' + tc.getBDms())
        title_b_pos.change('AZ: ' + tc.getADms())
        title_c_pos.change('C: ' + tc.getCDms())
        title_ra_dec.change(tc.getRaDec(-tc.getB(), tc.getA(), LATITUDE, LONGITUDE))
    except:
        print('Nan exception')
    line = 'A' + str(tc.getA()) + ' B' + str(tc.getB()) +' C' + str(tc.getC()) + '\n'
    tracker.write(line.encode('UTF-8'))
    #print(line)
    time.sleep(0.02)
    pygame.display.flip()

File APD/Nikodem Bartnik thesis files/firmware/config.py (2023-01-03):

PIN_LED_1 = 6
PIN_LED_2 = 7
PIN_LED_3 = 8
PIN_BUZZER = 9
PIN_M1_ENABLE = 24
PIN_M1_STEP = 23
PIN_M1_DIR = 22
PIN_M2_ENABLE = 21
PIN_M2_STEP = 20
PIN_M2_DIR = 19
PIN_M3_ENABLE = 18
PIN_M3_STEP = 17
PIN_M3_DIR = 16

M1_REVERSE_DIR = False
M2_REVERSE_DIR = True
M3_REVERSE_DIR = True

#small base gear: 10 teeth
#big base gear: 50 teeth
#motor steps: 200 steps/rev
#microstepping: 1/16
#result: 16 000 steps/rev so 44.44 steps per degree
A_STEPS_PER_DEGREE = 44
#small pulley: 16 teeth
#big pulley: 70 teeth
#motor steps: 200 steps/rev
#microstepping: 1/16
#result: 14 000 steps/rev so 38.89 steps per degree
B_STEPS_PER_DEGREE = 39
C_STEPS_PER_DEGREE = 39

DELAY_BETWEEN_STEPS = 0.002

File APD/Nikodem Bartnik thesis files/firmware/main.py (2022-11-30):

import time, sys
from machine import Pin, PWM
from StepperMotor import StepperMotor as Motor
from config import *
from Tracker import Tracker as Tracker

    
def readCommand():
    global pos_a, pos_b, pos_c
    cm_list = sys.stdin.readline().strip().split(' ')
    print(cm_list)
    if cm_list[0] != '':
        targets = [tracker.getA(), tracker.getB(), tracker.getC()]
        if len(cm_list) >= 1:
            if cm_list[0][0] == 'A':
                print('Moving A axis by: ', float(cm_list[0][1:]), ' deg\n')
                targets[0] = float(cm_list[0][1:]) * A_STEPS_PER_DEGREE
                
        if len(cm_list) >= 2:
            if cm_list[1][0] == 'B':
                print('Moving B axis by: ', float(cm_list[1][1:]), ' deg\n')
                targets[1] = float(cm_list[1][1:]) * B_STEPS_PER_DEGREE
        if len(cm_list) >= 3:
            if cm_list[2][0] == 'C':
                print('Moving C axis by: ', float(cm_list[2][1:]), ' deg\n')
                targets[2] = float(cm_list[2][1:]) * C_STEPS_PER_DEGREE
                
        tracker.moveTo(targets[0], targets[1], targets[2])
        

tracker = Tracker()
while(1):
    readCommand()

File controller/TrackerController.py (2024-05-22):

import TrackerMath as tm
import numpy as np
import datetime
from astropy.coordinates import EarthLocation, AltAz, SkyCoord
from astropy.time import Time
import astropy.units as u

class TrackerController:
    def __init__(self):
        self.origin_vec_y = np.array([0, 1, 0], dtype=np.longdouble)
        self.origin_vec_x = np.array([1, 0, 0], dtype=np.longdouble)
        self.origin_vec_z = np.array([0, 0, 1], dtype=np.longdouble)

        self.ref_vec_x = self.origin_vec_x
        self.ref_vec_y = self.origin_vec_y
        self.ref_vec_z = self.origin_vec_z       
    
        self.polar_vec_x = self.origin_vec_x
        self.polar_vec_y = self.origin_vec_y
        self.polar_vec_z = self.origin_vec_z

        self.tracker_vec_x = self.origin_vec_x
        self.tracker_vec_y = self.origin_vec_y
        self.tracker_vec_z = self.origin_vec_z
        

    def polarAlign(self):
        self.polar_vec_x = self.tracker_vec_x
        self.polar_vec_y = self.tracker_vec_x
        self.polar_vec_z = self.tracker_vec_z


    def rotateAltitude(self, a):
        self.tracker_vec_x = tm.rotateAroundAxis(self.tracker_vec_x, self.tracker_vec_y, a)

    def rotateAzimuth(self, a):
        self.tracker_vec_x = tm.rotateAroundAxis(self.tracker_vec_x, self.origin_vec_z, a)
        self.tracker_vec_y = tm.rotateAroundAxis(self.tracker_vec_y, self.origin_vec_z, a)
        self.tracker_vec_z = tm.rotateAroundAxis(self.tracker_vec_z, self.origin_vec_z, a)

        self.ref_vec_x = tm.rotateAroundAxis(self.ref_vec_x, self.origin_vec_z, a)
        self.ref_vec_y = tm.rotateAroundAxis(self.ref_vec_y, self.origin_vec_z, a)
        self.ref_vec_z = tm.rotateAroundAxis(self.ref_vec_z, self.origin_vec_z, a)

    def rotateField(self, x):
        self.tracker_vec_y = tm.rotateAroundAxis(self.tracker_vec_y, self.tracker_vec_x, x)
        self.tracker_vec_z = tm.rotateAroundAxis(self.tracker_vec_z, self.tracker_vec_x, x)


    def track(self, angle):
        self.tracker_vec_x = tm.rotateAroundAxis(self.tracker_vec_x, self.polar_vec_x, angle)
        self.tracker_vec_y = tm.rotateAroundAxis(self.tracker_vec_y, self.polar_vec_x, angle)
        self.tracker_vec_z = tm.rotateAroundAxis(self.tracker_vec_z, self.polar_vec_x, angle)


    def getA(self):
        return np.sign(self.tracker_vec_x[1])*np.arccos(self.tracker_vec_x[0]/(np.sqrt(pow(self.tracker_vec_x[0], 2) + pow(self.tracker_vec_x[1], 2)))) * 180/np.pi


    def getB(self):
        return np.arccos(self.tracker_vec_x[2]) * 180/np.pi - 90


    def getC(self):
        angle = np.degrees(np.arctan2(np.linalg.norm(np.cross(self.ref_vec_z, self.tracker_vec_z)), np.dot(self.ref_vec_z, self.tracker_vec_z)))
        if((np.cross(self.ref_vec_z, self.tracker_vec_z)[0] < 0 or self.tracker_vec_x[0] < 0) and not (np.cross(self.ref_vec_z, self.tracker_vec_z)[0] <= 0 and self.tracker_vec_x[0] <= 0)):
            angle = -angle
        return angle


    def getRefVecX(self):
        return self.origin_vec_x

    def getRefVecZ(self):
        return self.origin_vec_z

    def getPolarVecX(self):
        return self.polar_vec_x

    def getPolarVecZ(self):
        return self.polar_vec_z

    def getTrackerVecX(self):
        return self.tracker_vec_x

    def getTrackerVecZ(self):
        return self.tracker_vec_z

    def getADms(self):
        d, m, s = self.__decimalToDms(self.getA())
        return f"{d}° {m}' {s}\""

    def getBDms(self):
        d, m, s = self.__decimalToDms(self.getB())
        return f"{d}° {m}' {s}\""

    def getCDms(self):
        d, m, s = self.__decimalToDms(self.getC())
        return f"{d}° {m}' {s}\""

    def __decimalToDms(self, decimal):
        degrees = int(decimal)
        minutes = int((decimal - degrees) * 60)
        seconds = round((((decimal - degrees) * 60) - minutes) * 60, 2)
        return (degrees, minutes, seconds)
    
    def getRaDec(self, alt, az, latitude, longitude):
        ra, dec = self.altAzToRaDec(alt, az, latitude, longitude)
        ra_h = int(ra / 15)
        ra_m = int((ra / 15 - ra_h) * 60)
        ra_s = round((((ra / 15 - ra_h) * 60) - ra_m) * 60, 2)
        dec_d = int(dec)
        dec_m = int((dec - dec_d) * 60)
        dec_s = round((((dec - dec_d) * 60) - dec_m) * 60, 2)
        return f"{ra_h}h {ra_m}m {ra_s}s, {dec_d}° {dec_m}' {dec_s}\""
    
    def altAzToRaDec(self, alt, az, latitude, longitude):
        location = EarthLocation(lat=latitude * u.deg, lon=longitude * u.deg)
        time = Time(datetime.datetime.now())
        altaz = AltAz(alt=alt * u.deg, az=az * u.deg, location=location, obstime=time)
        skycoord = SkyCoord(altaz)
        ra = skycoord.icrs.ra.degree
        dec = skycoord.icrs.dec.degree
        return ra, dec

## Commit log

2022-11-05 values update
    [startrckr_pcb.kicad_sch]
2022-11-29 add pcb step file
    [startrckr_pcb.step]
2022-12-22 v4 added, v2 started
    [arm1_1.3mf, arm1_2.3mf, arm2.3mf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]
2022-12-25 rotation matrix fix, clean up
    [arm1.3mf, arm2.3mf, arm3.3mf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]
2023-01-03 added schematic.png
2023-01-03 added CAD files
    [arm2.3mf, base gear small.3mf, shaft1.3mf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]
2023-01-04 remove pcb backups
2023-01-11 clean up
    [6205 bearing holder.3mf, Base gear (57 teeth).3mf, Body6.3mf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]
2023-01-11 cad update
    [arm1.3mf, arm2.3mf, arm3.3mf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]
2023-04-23 documents uploaded to APD added
    [arm1.3mf, arm2.3mf, arm3.3mf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]
2023-04-23 fix wrong sign in tracking algorithm
    [controller.py]
2024-05-22 rotation matrix formula fix
    [TrackerMath.py]
2024-09-16 add more images/docs
    [1.dxf]
